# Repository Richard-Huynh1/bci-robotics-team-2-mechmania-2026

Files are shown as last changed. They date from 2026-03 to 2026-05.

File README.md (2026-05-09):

# Bluevale Collegiate Institute MechMania 2026 Team 2

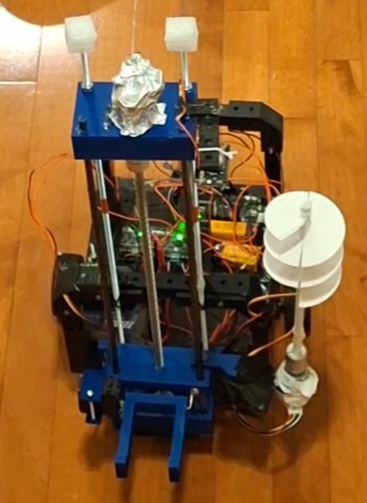
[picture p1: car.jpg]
MechMania car


- [Bluevale Collegiate Institute MechMania 2026 Team 2](#bluevale-collegiate-institute-mechmania-2026-team-2)
  - [Description](#description)
  - [Parts in the Controller](#parts-in-the-controller)
  - [Parts in the Car](#parts-in-the-car)
  - [Technical Notes](#technical-notes)
  - [Controller Instructions](#controller-instructions)
    - [Driving Mode](#driving-mode)
    - [Action Mode](#action-mode)
  - [Bill of Materials Link](#bill-of-materials-link)
  - [Demo Videos](#demo-videos)
  - [Team Members](#team-members)

## Description

This project was made possible by having two microcontrollers: one in the controller and one in the car. Communication between the controller and the car was made using a NRF24L01 in the controller (transmitter) and another NRF24L01 in the car (receiver).

In the Code folder, you will find all the code for the car and controller as well as wiring schematics. The schematics were made by a software called KiCad and the KiCad files are also located in this repository in case you would like to modify the schematics.

## Parts in the Controller

- 1 Arduino Uno R3 Clone
- 1 NRF24L01 with breakout board (wireless transmitter)
- 1 AM-JOYSTICK
- 2 9V batteries (one for NRF24L01 and one for UNO)
- 4 push buttons

## Parts in the Car

- 1 ELEGOO MEGA 2560 R3 Board (powered by 9V battery)
- 1 NRF24L01 with breakout board (wireless receiver)
- 2 motor drivers (MDD3A)
- 2 12V DC motors (400 RPM, higher torque, for wheels)
- 1 12V DC motor (400 RPM, higher torque, for drill)
- 1 12V DC motor (400 RPM, higher torque, for forklift)
- 1 11.1V 2200mAh Lipo Battery (power for the DC motors)
- 1 servo (MG996R, for platform tilt)
- 1 servo (MG996R, for platform drill tilt)
- 1 ESP32-CAM
- 4 AA batteries (powers servos and camera)

## Technical Notes

It is also important to note that the camera was not used as when the servo motors were powered, the camera turned off. To prevent this, in the future you may want to add a capacitor to the camera's 5V and GND pin. Also, 100 µF capacitors were used to connect the NRF24L01 power pins together in case of brownouts.

## Controller Instructions

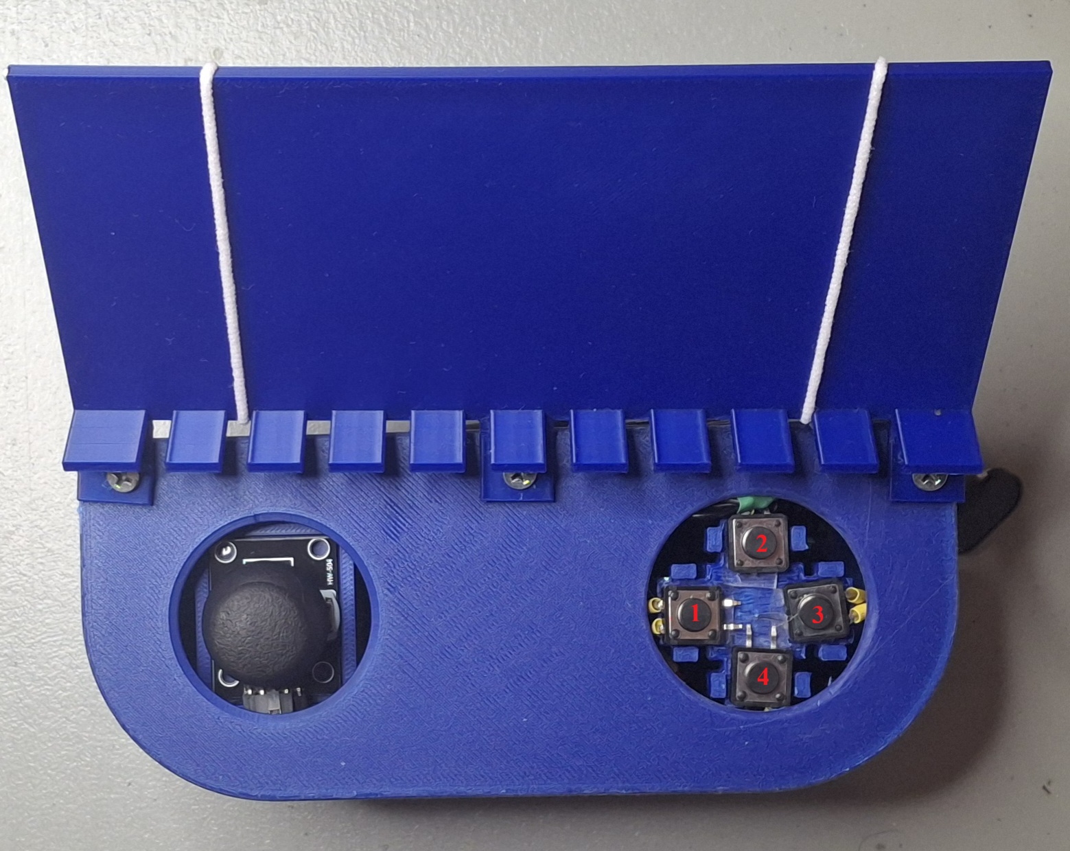
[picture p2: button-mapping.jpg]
Controller button mapping image


There are two modes for the forklift: driving mode and action mode. Switching between the modes is done by pressing button 2.

Here are the rest of the controls:

### Driving Mode

This is the default mode when everything is plugged in.

- **Joystick movement:** Move direction (must press gas to actually move)
- **Joystick press:** Spin clockwise (away from drill)
- **Button 1:** Quarter speed
- **Button 2:** Change mode
- **Button 3:** Full speed
- **Button 4:** Half speed

### Action Mode

- **Joystick up/down:** Forklift up/down
- **Joystick press:** Nothing
- **Button 1:** Drill up/down (tree planting)
- **Button 2:** Change mode
- **Button 3:** Tilt platform 55 degrees/to neutral (mainly for sharp shooter)
- **Button 4:** Spin drill (tree planting)

## Bill of Materials Link

Here is the link to the bill of materials: [Link](https://docs.google.com/spreadsheets/d/1pDJakI2937subbM1QwxTJR9V5k_md9ht5O3d4-HkXg0/edit?usp=sharing)

## Demo Videos

Here is a link to the Google Drive folder containing demo videos of the car: [Link](https://drive.google.com/drive/folders/1xLPtX33iqkmJ1HCEXODp4CY6vhk1JXrE?usp=drive_link)

## Team Members

- Slobodan Zivkovic (Mr. Zee, awesome teacher)
- Sravya Vemula
- Richard Huynh
- Rafael Alekberov
- Alex Zheng
- CJ Tejero
- Lia Jung
- Zonaira Junaid
- Louise Shin
- Yash Vakil

Thank you everyone for the effort. Especially in improvising to drive the car on dirt for the tree planting event.

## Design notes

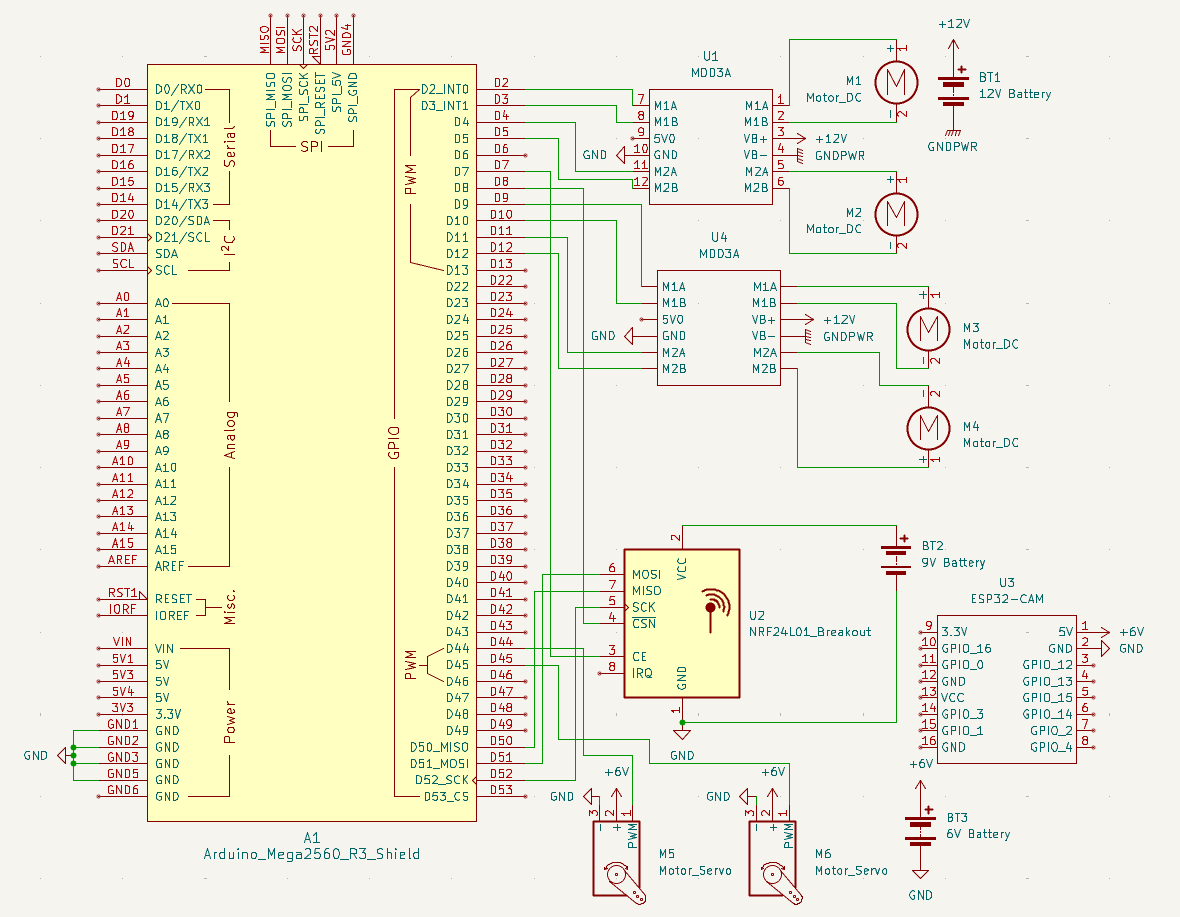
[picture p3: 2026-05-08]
Code/Car/schematic.png

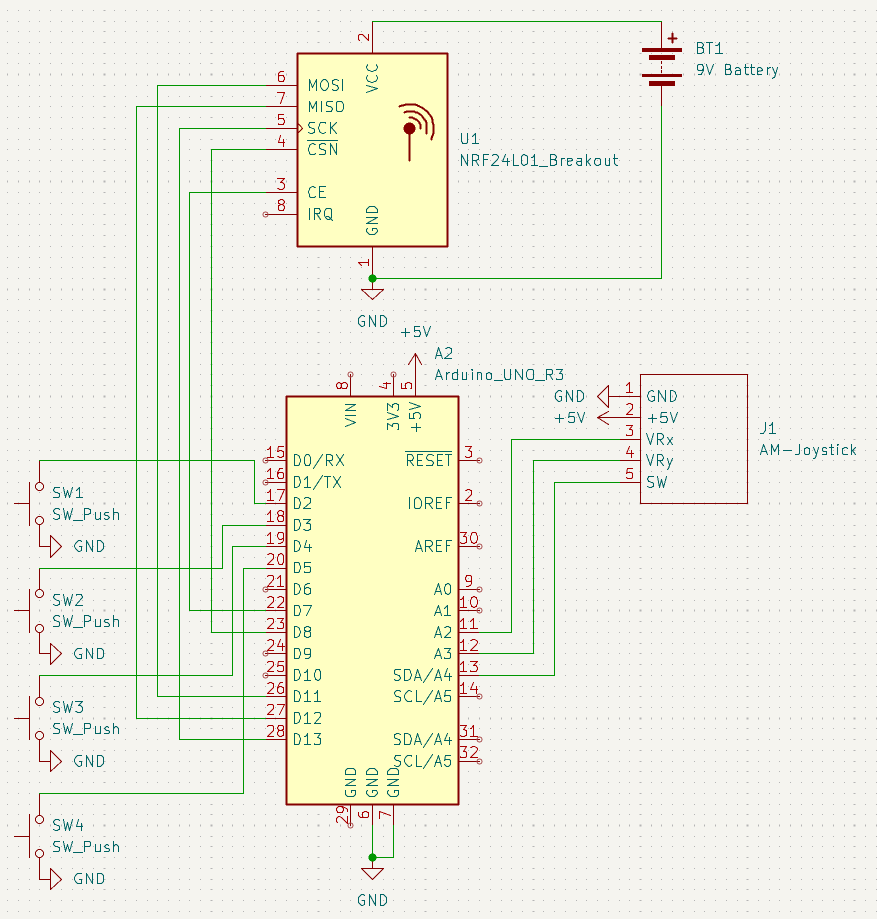
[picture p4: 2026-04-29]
Code/Controller/schematic.png

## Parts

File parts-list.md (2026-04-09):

# Parts List

This file contains all electrical parts as well as mechanical parts.

- [Parts List](#parts-list)
  - [Electrical Parts](#electrical-parts)
    - [Microcontrollers](#microcontrollers)
    - [Motors/Drivers](#motorsdrivers)
    - [Sensors/Inputs/Switches](#sensorsinputsswitches)
    - [Power](#power)
    - [Remote Control](#remote-control)
    - [Miscellaneous](#miscellaneous)

## Electrical Parts

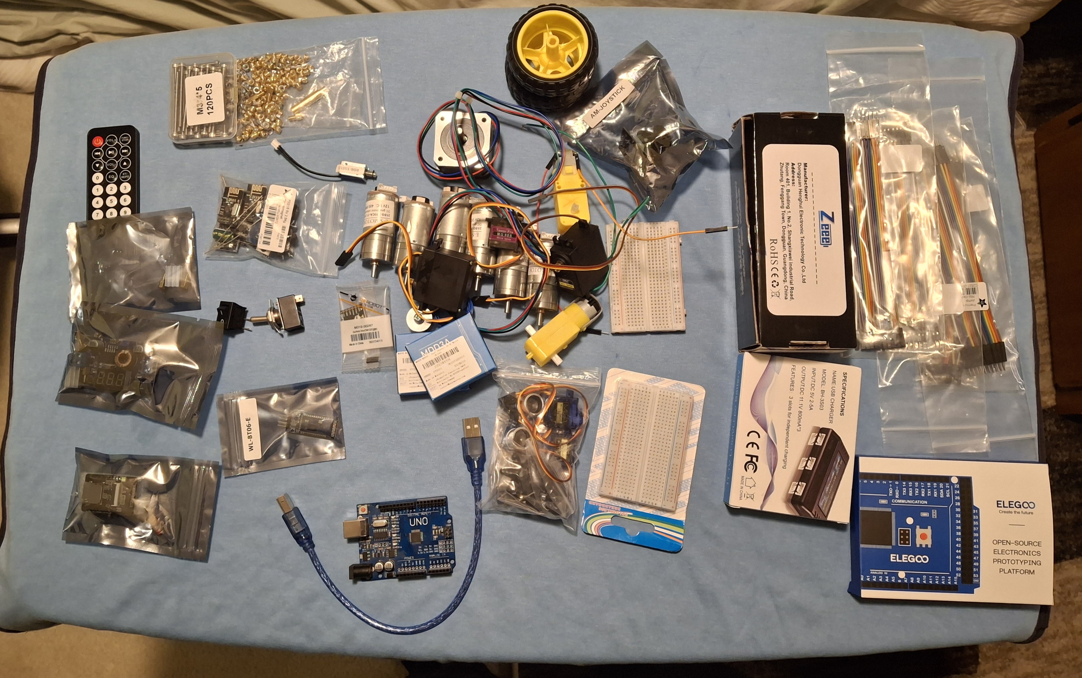
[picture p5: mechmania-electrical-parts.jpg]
MechMania electrical parts


### Microcontrollers

| Quantity | Part Name | Description | Information Link |
| :---: | :--- | :--- | :--- |
| 1 | Arduino Uno R3 Clone with USB Cable | A popular beginner-friendly 8-bit microcontroller board based on the ATmega328P. | [Visit documentation on the board](https://docs.arduino.cc/hardware/uno-rev3/) |
| 1 | ELEGOO MEGA 2560 R3 Board with USB Cable | A microcontroller based on the ATmega 2560. | [Instructions for use](https://m.media-amazon.com/images/I/91RAy+evkrL.pdf) |
| 1 | ESP-32 CAM | A camera that can interact with Wifi and Bluetooth with a 2MP resolution. | [Video streaming and face recognition](https://randomnerdtutorials.com/esp32-cam-video-streaming-face-recognition-arduino-ide/) |

### Motors/Drivers

| Quantity | Part Name | Part Number | Description | Information Link |
| :---: | :--- | :--- | :--- | :--- |
| 4 | 12V DC Motor with Encoder | 25SG-370CA-21.3-EN | 400 RPM motor with more torque. | [Motor datasheet](https://cdn.robotshop.com/rbm/a00a7635-653b-4220-aac9-b0c23c5c5e2c/9/937bc8fd-df7e-4549-84e7-739dc23aaa9d/c1a0ee55_25d-encoder-gear-motor-kits.pdf) |
| 2 | 12V DC Motor with Encoder | 25SG-370CA-4.4-EN  | 1930 RPM motor with less torque. | [Motor datasheet](https://cdn.robotshop.com/rbm/a00a7635-653b-4220-aac9-b0c23c5c5e2c/9/937bc8fd-df7e-4549-84e7-739dc23aaa9d/c1a0ee55_25d-encoder-gear-motor-kits.pdf) |
| 2 | Yellow TT Motor | N/A | DC gearbox motor. | [Product information](https://www.adafruit.com/product/3777) |
| 2 | Metal Gear Torque Digital Servo | MG996R | 55 g (weight) double ball bearing servo motor. | [Product information](https://www.diymore.cc/products/diymore-mg996r-metal-gear-high-speed-torque-servo-motor-digital-servo-55g-for-rc-helicopter-airplane-car-boat-robot-controls) |
| 2 | Miuzei Micro Servo Motor (Blue) | MS18 | A 9 g (weight) micro servo motor. | [Amazon listing](https://www.amazon.ca/Miuzei-Helicopter-Airplane-Remote-Control/dp/B07H85M78M) |
| 1 | Tower Pro Micro Servo (Black) | MG90S | A 13.4 g (weight) micro servo motor. | [Servo information](https://towerpro.com.tw/product/mg90s-3/) |
| 1 | Nema 17 Bipolar Stepper Motor | 17HS13-0404S1 | A stepper motor with a step angle of 1.8°, a shaft diameter of Φ5 mm and size 42 x 42 x 34 mm. | [Datasheet](https://www.omc-stepperonline.com/download/17HS13-0404S1.pdf) |
| 2 | Maker Dual Channel 3A DC Motor Driver | MDD3A | A motor driver that is able to run 3A per channel. | [Datasheet](https://mm.digikey.com/Volume0/opasdata/d220001/medias/docus/204/105090004_Web.pdf) |
| 1 | DFRobot 2x1.2 A DC Motor Driver | TB6612FNG | A motor driver that supports 1.2A per channel. | [Product description](https://wiki.dfrobot.com/dri0044/) |
| 1 | Stepper Motor Driver Module | A4988 | Microstepping motor driver with built-in translation. | [Datasheet](https://www.allegromicro.com/~/media/files/datasheets/a4988-datasheet.pdf) |

### Sensors/Inputs/Switches

| Quantity | Part Name | Part Number | Description | Information Link |
| :---: | :--- | :--- | :--- | :--- |
| 1 | Ultrasonic Ranging Module | HC-SR04 | Used to measure distance. | [Datasheet](https://cdn.sparkfun.com/datasheets/Sensors/Proximity/HCSR04.pdf) |
| 9 | Large Button | | | |
| 2 | Switches | | | |
| 1 | AM-JOYSTICK | | | [Product description](https://abra-electronics.com/robotics-embedded-electronics/arduino-shields/audio-video-game-shields/am-joystick-analog-joystick-module.html) |

### Power

| Quantity | Part Name | Part Number | Description | Information Link |
| :---: | :--- | :--- | :--- | :--- |
| 2 | Zeee 11.1V 2200mAh Lipo Battery 3S Shorty Lipo 50C Soft Pack RC Battery with Deans Plug | | An 11.1V lithium polymer battery pack. | [Amazon listing](https://www.amazon.ca/Zeee-2200mAh-Battery-Airplane-Helicopter/dp/B0D9QKR1WJ) |
| 1 | USB Charger | BH-3S03 | Used to charge the Lipo batteries. | [Product description](https://abra-electronics.com/batteries-holders/battery-chargers-testers/bat-charger-15-usb-3s-lipo-battery-pack-charger-11.1v-800ma.html) |
| 2 | 12V Regulator | LM2575T-12  | Used to reduce a higher input voltage to a lower stable output voltage. | [Datasheet](https://www.ti.com/lit/ds/symlink/lm2575-n.pdf) |
| 1 | DC-DC High power LED Driver with Red Voltmeter Adjustable Step-down Charger Module | HW-316E | Converts larger DC voltages into smaller ones. | [RFID LIFE listing](https://shop.rfid-life.com/products/hw-316e-xl4015-5a-75w-dc-dc-high-power-led-driver-with-red-voltmeter-adjustable-step-down-charger-module) |

### Remote Control

| Quantity | Part Name | Part Number | Description | Information Link |
| :---: | :--- | :--- | :--- | :--- |
| 1 | IR Remote Controller | | | [Product listing](https://www.tinyosshop.com/index.php?route=product/product&product_id=665) |
| 2 | NRF24L01 (Transceiver and Receiver) | | Used to make wireless communcation between two Arduino boards. | [Tutorial](https://howtomechatronics.com/tutorials/arduino/arduino-wireless-communication-nrf24l01-tutorial/) |
| 1 | Bluetooth Module 1 | WL-BT06-E | This Wireless Bluetooth Transceiver Slave Module allows your device to both send or receive the TTL data via Bluetooth technology without connecting a serial cable to your computer. | [Product listing](https://abra-electronics.com/wireless/wireless-bluetooth-en/wl-bt06-e-rf-wireless-bluetooth-transceiver-slave-module-rs232-ttl-to-uart-converter-and-adapter-for-ardu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) |
| 1 | Bluetooth Module 2 | HC-06 | A slave-only module. | [Tutorial with Arduino](https://www.martyncurrey.com/arduino-and-hc-06-zs-040/) |

### Miscellaneous

| Quantity | Part Name | Part Number | Description | Information Link |
| :---: | :--- | :--- | :--- | :--- |
| 2 | NPN Transistor | P2N222A and BC547 | | [Datasheet P2N222A](https://www.onsemi.com/pdf/datasheet/p2n2222a-d.pdf), [BC547 information](https://www.seeedstudio.com/blog/2020/09/10/bc547-transistor-basic-knowledge-pinout-and-application/) |
| 2 | PNP Transistor | BC557B | | [Datasheet](https://www.farnell.com/datasheets/296678.pdf) |
| 1 | 50V 100uF Capacitor | | | |
| 1 | 10V 1500uF Capacitor | | | |
| 1 | 25V 680uF Capacitor | | | |
| 4 | Diode | | | |
| 1 | Electromagnet | | | [Product listing](https://www.adafruit.com/product/3872?srsltid=AfmBOopdHWw1D8Pn7Wg_neplB1FX3qU4yjKQzFZ2b9Pweh9NQRtVLy13) |
| 1 | ROB-11015 (5V Solenoid) | ZH0-0420S-05A4.5  | | [Datasheet](https://cdn.sparkfun.com/datasheets/Robotics/ZHO-0420S-05A4.5%20SPECIFICATION.pdf) |
| 2 | Small Breadboard | | | |
| A lot | Male to Female Jumper Wire  | | | |
| A lot | Male to Male Jumper Wire | | | |

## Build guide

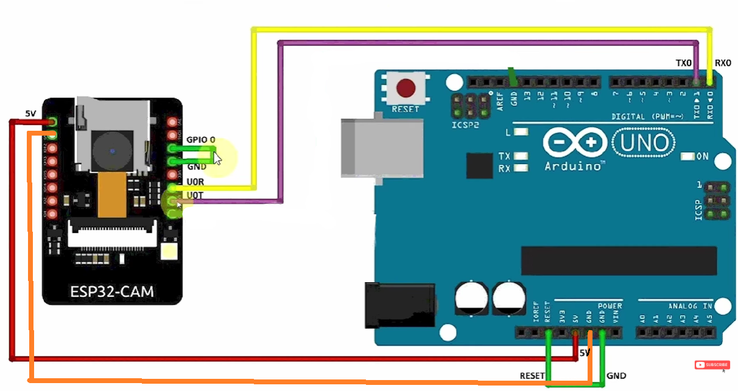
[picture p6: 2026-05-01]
BciTeam2CamCode/camera-wiring-upload-code.png

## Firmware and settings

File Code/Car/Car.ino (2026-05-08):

/*
Links used:
- https://www.cytron.io/tutorial/getting-started-mdd3a-makerdrive-motor-driver-using-arduino
- https://howtomechatronics.com/tutorials/arduino/arduino-wireless-communication-nrf24l01-tutorial/
- https://projecthub.arduino.cc/hibit/using-joystick-module-with-arduino-0ffdd4
- https://howtomechatronics.com/how-it-works/how-servo-motors-work-how-to-control-servos-using-arduino/

See image (for joystick):
- https://components101.com/sites/default/files/inline-images/Joystick-Module-Analog-Output.png
*/

#include <SPI.h>
#include <nRF24L01.h>
#include <RF24.h> 
#include <CytronMotorDriver.h>
#include <Servo.h>
#include <string.h>

#define MAX_SPEED 255
#define HALF_SPEED 128
#define QUARTER_SPEED 64

CytronMD motorRight(PWM_PWM, 2, 3);
CytronMD motorLeft(PWM_PWM, 4, 5);
CytronMD motorDrill(PWM_PWM, 9, 10);
CytronMD motorForklift(PWM_PWM, 11, 12);

Servo platformServo;
Servo drillServo;

bool platformTilted = false;
bool drillDown = false;

typedef struct {
  short x;
  short y;
  bool joystickPressed;
  bool btn1Pressed;
  bool btn2Pressed;
  bool btn3Pressed;
  bool btn4Pressed;
  char password[6];
} DataPackage;

DataPackage data;
bool isDriving = true;

RF24 radio(7, 8); // CE, CSN

// Speeds are 0-255 PWM
int speedLeft = 255;
int speedRight = 255;
const byte address[6] = "BCIT2";

void move(short y, short x);
void moveForklift(short x);

void setup() {
  Serial.begin(9600);

  platformServo.attach(45);
  drillServo.attach(44);

  platformServo.write(0);
  drillServo.write(0);

  radio.begin();
  radio.setChannel(108);
  radio.openReadingPipe(0, address);
  radio.setPALevel(RF24_PA_MIN);
  radio.startListening();
}

void loop() {
  if (radio.available()) {
    radio.read(&data, sizeof(data));
    if (strcmp(data.password, "BCIT2")) return;

    if (data.btn4Pressed) {
      isDriving = !isDriving;
      speedLeft = 0;
      speedRight = 0;
      motorLeft.setSpeed(speedLeft);
      motorRight.setSpeed(speedRight);
      motorDrill.setSpeed(0);
      motorForklift.setSpeed(0);
    }

    if (isDriving) {
      if (data.btn1Pressed) {
        speedLeft = MAX_SPEED;
        speedRight = MAX_SPEED;
        move(data.y, data.x);
      } else if (data.btn2Pressed) {
        speedLeft = HALF_SPEED;
        speedRight = HALF_SPEED;
        move(data.y, data.x);
      } else if (data.btn3Pressed) {
        speedLeft = QUARTER_SPEED;
        speedRight = QUARTER_SPEED;
        move(data.y, data.x);
      } else if (data.joystickPressed) {
        speedLeft = HALF_SPEED;
        speedRight = -HALF_SPEED;
        motorLeft.setSpeed(speedLeft);
        motorRight.setSpeed(speedRight);
      } else {
        speedLeft = 0;
        speedRight = 0;
        motorLeft.setSpeed(speedLeft);
        motorRight.setSpeed(speedRight);
      }
    } else {
      moveForklift(data.x);
      // Tilt platform
      if (data.btn1Pressed) {
        if (platformTilted) {
          platformServo.write(0);
        } else {
          platformServo.write(55);
        }
        platformTilted = !platformTilted;
      }
      // Spin drill
      if (data.btn2Pressed) {
        motorDrill.setSpeed(-HALF_SPEED);
      } else {
        motorDrill.setSpeed(0);
      }
      // Drill up/down
      if (data.btn3Pressed) {
        if (drillDown) {
          drillServo.write(0);
        } else {
          drillServo.write(180);
        }
        drillDown = !drillDown;
      }
    }

    char buffer[128];
    snprintf(buffer, sizeof(buffer),
      "(%d, %d), joystick pressed: %s, 1: %s, 2: %s, 3: %s, 4: %s, password: %s",
       data.x, data.y, data.joystickPressed ? "true" : "false",
       data.btn1Pressed ? "true" : "false", data.btn2Pressed ? "true" : "false",
       data.btn3Pressed ? "true" : "false", data.btn4Pressed ? "true" : "false",
       data.password
    );

    Serial.println(buffer);
  }
}

void move(short y, short x) {
  // Quadrant 1
  if (y > 0 && x > 0) {
    speedRight *= abs(atan(x / (double)y)) / HALF_PI;
  // Quadrant 2
  } else if (y < 0 && x > 0) {
    speedLeft *= abs(atan(x / (double)y)) / HALF_PI;
  // Quadrant 3
  } else if (y < 0 && x < 0) {
    speedLeft *= -1;
    speedRight *= -1;

    speedRight *= abs(atan(x / (double)y)) / HALF_PI;
    Serial.println(speedRight);
  // Quadrant 4
  } else if (y > 0 && x < 0) {
    speedLeft *= -1;
    speedRight *= -1;

    speedLeft *= abs(atan(x / (double)y)) / HALF_PI;
    Serial.println(speedLeft);
  // On axes
  // Stationary
  } else if (y == 0 && x == 0) {
    speedLeft = 0;
    speedRight = 0;
  // Left turn
  } else if (y > 0 && x == 0) {
    speedRight = 0;
  // Right turn
  } else if (y < 0 && x == 0) {
    speedLeft = 0;
  // Reverse
  } else if (y == 0 && x < 0) {
    speedLeft *= -1;
    speedRight *= -1;
  }
  
  motorLeft.setSpeed(speedLeft);
  motorRight.setSpeed(speedRight);
}

void moveForklift(short x) {
  // Forklift up
  if (x > 0) {
    motorForklift.setSpeed(MAX_SPEED);
  // Forklift down
  } else if (x < 0) {
    motorForklift.setSpeed(-MAX_SPEED);
  // Stop forklift
  } else {
    motorForklift.setSpeed(0);
  }
}

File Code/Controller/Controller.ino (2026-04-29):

/*
Links used:
- https://howtomechatronics.com/tutorials/arduino/arduino-wireless-communication-nrf24l01-tutorial/
- https://projecthub.arduino.cc/hibit/using-joystick-module-with-arduino-0ffdd4
*/

#include <SPI.h>
#include <nRF24L01.h>
#include <RF24.h>

#define ANALOG_X_PIN A2
#define ANALOG_Y_PIN A3
#define ANALOG_BUTTON_PIN A4

#define ANALOG_X_CORRECTION 128
#define ANALOG_Y_CORRECTION 128

#define JOYSTICK_DEADZONE 40  // Minimum change to trigger send

#define BUTTON_PIN_1 2  // Full gas/forklift up
#define BUTTON_PIN_2 3  // Half gas/forklift down
#define BUTTON_PIN_3 4  // Spin drill
#define BUTTON_PIN_4 5  // Switch modes

typedef struct {
  short x;
  short y;
  bool joystickPressed;  // Rotate in one place
  bool btn1Pressed;
  bool btn2Pressed;
  bool btn3Pressed;
  bool btn4Pressed;
  char password[6];
} DataPackage;

DataPackage lastSent = {0, 0, false, false, false, false, false, "BCIT2"};  // Keep track of last values

RF24 radio(7, 8);  // CE, CSN

const byte address[6] = "BCIT2";

void setup() {
  Serial.begin(9600);
  pinMode(ANALOG_BUTTON_PIN, INPUT_PULLUP); 
  pinMode(BUTTON_PIN_1, INPUT_PULLUP);
  pinMode(BUTTON_PIN_2, INPUT_PULLUP);
  pinMode(BUTTON_PIN_3, INPUT_PULLUP);
  pinMode(BUTTON_PIN_4, INPUT_PULLUP);
  radio.begin();
  radio.setChannel(108);
  radio.openWritingPipe(address);
  radio.setPALevel(RF24_PA_MIN);
  radio.stopListening();
}

void loop() {
  DataPackage current;
  current.x = readAnalogAxisLevel(ANALOG_X_PIN) - 128;
  current.y = readAnalogAxisLevel(ANALOG_Y_PIN) - 128;
  current.joystickPressed = isAnalogButtonPressed(ANALOG_BUTTON_PIN);
  current.btn1Pressed = digitalRead(BUTTON_PIN_1) == LOW;
  current.btn2Pressed = digitalRead(BUTTON_PIN_2) == LOW;
  current.btn3Pressed = digitalRead(BUTTON_PIN_3) == LOW;
  current.btn4Pressed = digitalRead(BUTTON_PIN_4) == LOW;
  strcpy(current.password, "BCIT2");

  if (-5 <= current.x && current.x <= 5) {
    current.x = 0;
  }
  if (-5 <= current.y && current.y <= 5) {
    current.y = 0;
  }

  // Check if joystick moved beyond deadzone or button changed
  bool xChanged = abs(current.x - lastSent.x) >= JOYSTICK_DEADZONE;
  bool yChanged = abs(current.y - lastSent.y) >= JOYSTICK_DEADZONE;
  bool btn1Changed = current.btn1Pressed != lastSent.btn1Pressed;
  bool btn2Changed = current.btn2Pressed != lastSent.btn2Pressed;
  bool btn3Changed = current.btn3Pressed != lastSent.btn3Pressed;
  bool btn4Changed = current.btn4Pressed != lastSent.btn4Pressed;
  bool joystickChanged = current.joystickPressed != lastSent.joystickPressed;

  if (xChanged || yChanged || joystickChanged
    || btn1Changed || btn2Changed || btn3Changed || btn4Changed)
  {
    bool ok = radio.write(&current, sizeof(current));
    if (!ok) {
      Serial.println("Send failed!");
    }
    lastSent = current;
  }

  delay(100);
}

byte readAnalogAxisLevel(int pin) {
  return map(analogRead(pin), 0, 1023, 0, 255);
}

bool isAnalogButtonPressed(int pin) {
  return digitalRead(pin) == 0;
}

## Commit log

2026-03-31 Add joystick communication and gas buttons (#2)
    * Implement hello world communication between microcontrollers
    * Add basic joystick communication code
    * Add gas buttons (#1)
    * Implement button state detection and transmission
    Added button handling to transmit button press state.
    * Add gas button
    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
2026-04-06 Add KiCad files and separate schematics for the transmitter and receiver (#3)
    [Receiver.kicad_pcb, Receiver.kicad_sch, Transmitter.kicad_pcb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]
2026-04-09 Add documentation of different 12V motors (#4)
2026-04-16 Update schematics and make car run (#5)
    [Receiver.kicad_sch]
2026-04-29 Add more buttons, modify schematic, and change code (#6)
    * Add more buttons, update schematic, improve drive system
    * Change button pins, schematic, and add quarter speed
    [Receiver.kicad_sch, Transmitter.kicad_sch]
2026-05-01 Add camera to robot (#7)
    * Add camera code and schematic to upload code from Arduino UNO to camera
    * Add camera to receiver schematic
    [Receiver.kicad_sch]
2026-05-08 Add forklift functionality (#8)
    * Add code to allow for forklift, drill and platform movement
    * Update receiver schematic and fine-tuned receiver code
    * Change rotation direction of drill and platform tilt to 55 degrees
    [Receiver.kicad_sch]
2026-05-08 Add controller instructions (#9)
    * Update README.md with controls
    * Specify driving mode spin in one place direction
    * Add table of contents and bill of materials to README.md
    * Change spin in one place direction
2026-05-09 Rename files and add documentation in README.md (#10)
    [Car.kicad_pcb, Car.kicad_sch, Controller.kicad_pcb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]
